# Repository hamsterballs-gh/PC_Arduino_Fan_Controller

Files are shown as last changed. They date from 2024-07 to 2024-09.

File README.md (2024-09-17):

# PC_Arduino_Fan_Controller
Arduino Fan and RGB Controller

A repository in shambles!
This is heavily under construction and many things are yet to be added/fixed/sorted out.

This project is for an Arduino-Nano based Fan and RGB controller, to fit in an old repurposed DVD Drive cage.

Hardware features:
- It can control 6 fans with PWM, of which channels 1-4 can use variable voltage DC.
- It controls three separate 12v RGB channels. 2 are 12v, and 1 is 5v for LEDs to fit in the case.
- RGB hard drive light - Two 2-pin connectors are used to use 2 HDD light inputs (I have a SAS card with a HDD light output). This controls the second 5v output.
- Support for 4 temperature sensors.
- Infra-red remote support, currently set to use the 44 button remotes that come with cheap Chinese RGB kits.
- Light sensor for auto LCD screen dimming.
- 16x2 I2C LCD display, to display messages.
- Read fan RPM from all channels.
- Serial communication to PC over USB.
- FRAM and EEPROM used for storing settings. EEPROM is used as a backup but must be restored manually with a serial command.
- A buzzer for alerts. I have not programmed this yet.
- Red LED indicator, typically lit up for serial transfers, IR commands and it will flash if the scheduler runs behind.
- Real-time clock so the fan controller can display the time even after being powered off.

Code features:
- Can set custom fan profiles, set using an average of 8 temperature inputs (4 built-in and overrideable, 8 can be sent from the computer).
    - Specifically, fans can all be set from 0 to 100%, regardless of temperature.
- Can set custom RGB profiles, including a 10 colour sequence, or a range of random values.
- Can send messages to the LCD display.
- Can custom strings for the fan controller.
- Can read fan RPM and temperature values to PC.

State of things:
- Most of the Arduino code is feature complete.
- The PCB design needs to be updated, but can be bodged to a working state.
- Component values are often incorrect. A parts list needs to be made.
- Basic Python Serial interaction is mostly working.

Next major tasks:
- Improve documentation and add a creation/installation guide.
- Create a GUI in Python to enable easy setting of RGB and fan profiles, and read data.

If you have taken an interest in this project and something's not right, please raise an issue.
That way I should get an email and I will respond as soon as I can.

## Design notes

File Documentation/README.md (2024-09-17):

# Documentation

This is where the documentation lives.
Information such as how to use the RGB remote, installation and hardware modifications.

### Arduino Modifications
- Information on modifications suggested for the Arduino Nano

### Remote Control
- A brief description on what every button does

### Components
- A list of components required for the project

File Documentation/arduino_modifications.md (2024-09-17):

# Arduino Modifications

## Disable auto-reset on serial connection
- The Arduino Nano will reset on any serial connection being established.
- Remove the indicated capacitor to disable this.
- Tweezers and a soldering iron are recommended.
- Note that the exact location of the capacitor can differ on Nano variants.

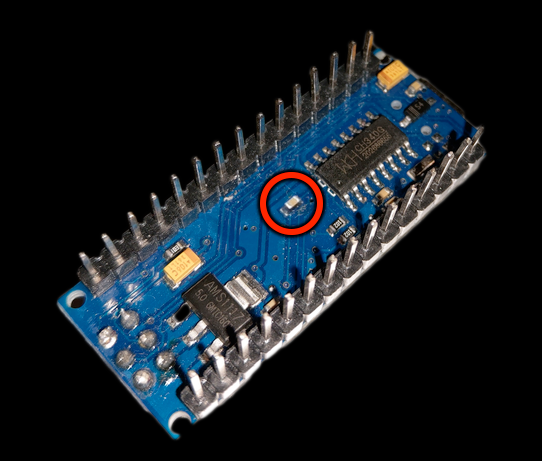
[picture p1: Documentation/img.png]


## Prevent USB backpower to 5v and 12v rails
- The Arduino Nano allows the USB input to backpower the 5v and Vin pins.
- If connected with USB to a computer where the USB ports remain powered on shutdown, backpowering can occur.
- This may damage the Arduino and/or the computer, or result in unwanted behaviour.
- Remove the indicated diode to prevent this.
- Tweezers and a soldering iron are recommended.
- Note that the exact location of the diode can differ on Nano variants.

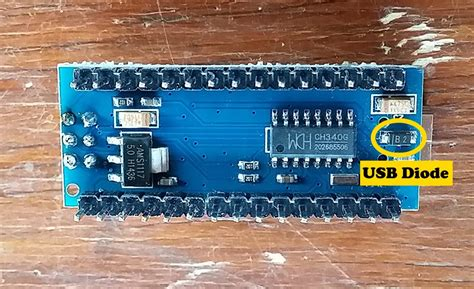
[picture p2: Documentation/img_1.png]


## Warning
- Please note that these changes are easy to perform, but reversing them takes skill in small-scale soldering.
- For the regular user, please understand that this is essentially a permanent modification of the Nano.

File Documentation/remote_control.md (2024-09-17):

# Remote Control Scheme

## Using: RGB 44 button remote

### Brightness Up:
- Increase brightness on selected RGB channel
- If all channels selected, channels 2 and 3 will be set to power LED channel brightness
### Brightness Down:
- Decrease brightness on selected RGB channel
- If all channels selected, channels 2 and 3 will be set to power LED channel brightness
### Pause:
- Pauses and resumes dynamic RGB profiles on selected channels
### Power:
- Turns on/off selected RGB channel
- Power and HDD LED outputs will be set to minimum brightness, but not off
- If all channels selected, channels 2 and 3 will be set to power LED channel power state
### Colour buttons:
- Load the set profile for the button on the selected RGB channels
- By default, this will be colours to closely match the buttons, and will be static
### Red/Green/Blue up buttons:
- If a static RGB profile is selected, the Red/Green/Blue value will be increased
- If a random colour, dynamic RGB channel is selected, this will increase the minimum random value of the associated chosen colour
### Quick:
- Speed will be increased on selected RGB channels using a dynamic RGB profile
### Red/Green/Blue down buttons:
- If a static RGB profile is selected, the Red/Green/Blue value will be decreased
- If a random colour, dynamic RGB channel is selected, this will decrease the minimum random value of the associated chosen colour
### Slow:
- Speed will be decreased on selected RGB channels using a dynamic RGB profile
### DIY 1/2/3:
- Select individual RGB channels 1/2/3
### Auto:
- Change inbuilt LCD display to next mode
### DIY 4:
- If RGB channels 2 or 3 are selected, set these channels to match RGB of channel 1
- Brightness of the channel will remain unchanged
### DIY 5:
- If RGB channel 3 is selected, set this channel to match RGB of channel 2
- Brightness of the channel will remain unchanged
### DIY 6:
- Select all RGB channels
### Flash:
- Load the 'flash' RGB profile on the selected RGB channels
### Jump 3:
- Load the RGB profile on the selected RGB channels
- By default, this will display red, green and blue colours in a repeating pattern
### Jump 7:
- Load the RGB profile on the selected RGB channels
- By default, this will display a random colour on each colour change
### Fade 3:
- Load the RGB profile on the selected RGB channels
- By default, this will display red, green and blue in a repeating pattern with a smooth transition
### Fade 7:
- Load the RGB profile on the selected RGB channels
- By default, this will display a random colour on each colour change with a smooth transition

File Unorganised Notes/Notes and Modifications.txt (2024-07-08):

########################################
# Arduino Fan Controller Modifications #
########################################

Things that aren't in the other notes but may be important:

1) Laziness
	Currently, my organisation on this project is in shambles.
	Documentation is imaginary, at best.

2) Backpowering
	If the connected USB port remains powered when PC is off, the Arduino will remain on.
	Add a diode from the 12v molex to Vin on the Arduino
	- this will prevent backpowering to the PC 12v rail.
	Ideally, a reset trigger needs to be put in place when the 12v powers up on computer reboot.

3) Wire bodging
	As shown in one of the pictures, the output wiring from the ATTiny85s are wrong.
	This requires a fix in the PCB design but this hasn't been done yet.

4) Fritzing
	The Adafruit parts library was used.
	This may have been updated.

5) Python libraries
	Installation of psutil and GPUtil are required for pc_status_130 to display all information.
	PySerial is used.

6) Arduino libraries
	LCD by Blackhawk
	Adafruit BusIO and PWM driver for PCA9685
	IRRemote

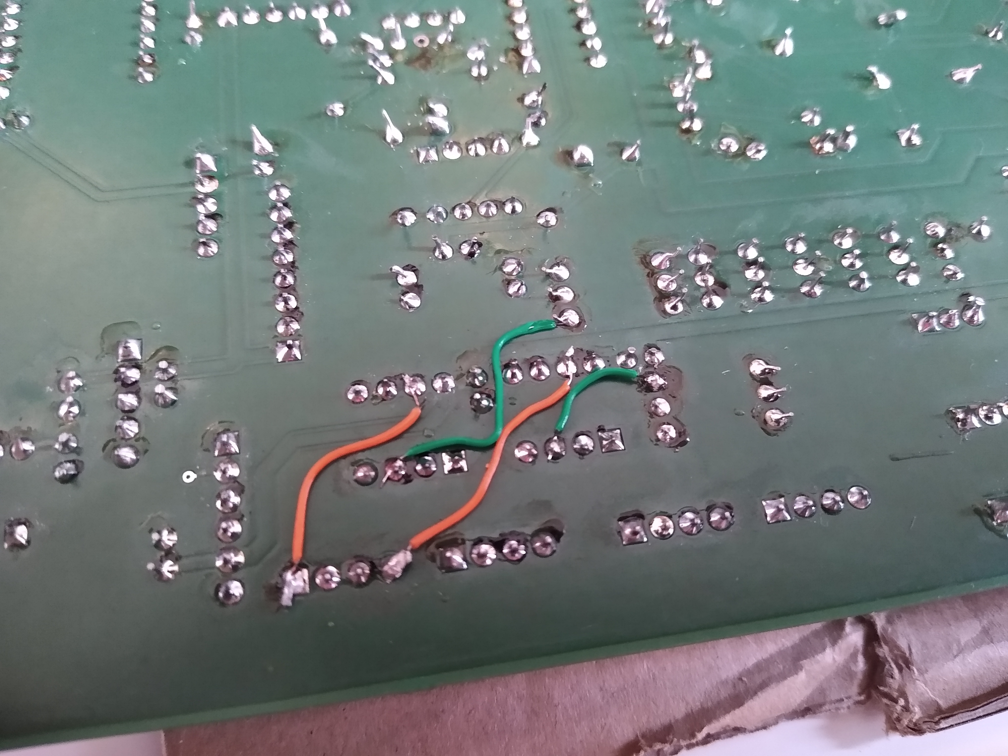
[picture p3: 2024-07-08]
Pictures/ATTiny85 bodge wires.jpg

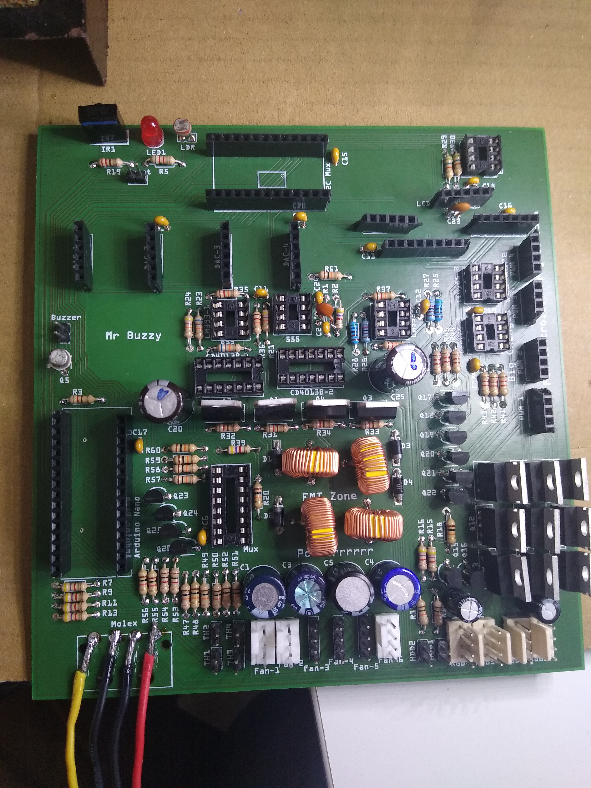
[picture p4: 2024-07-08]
Pictures/Semi-populated PCB.jpg

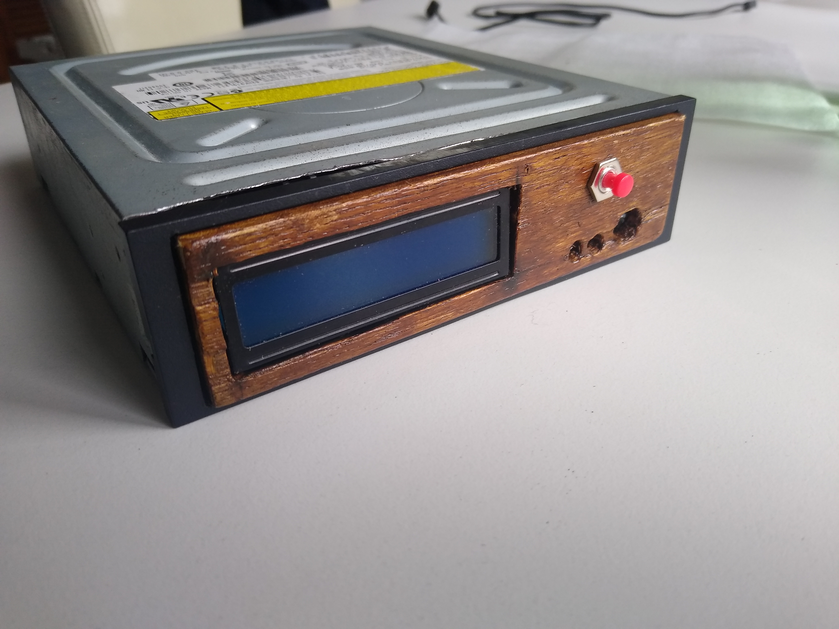
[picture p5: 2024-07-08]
Pictures/DVD housing.jpg

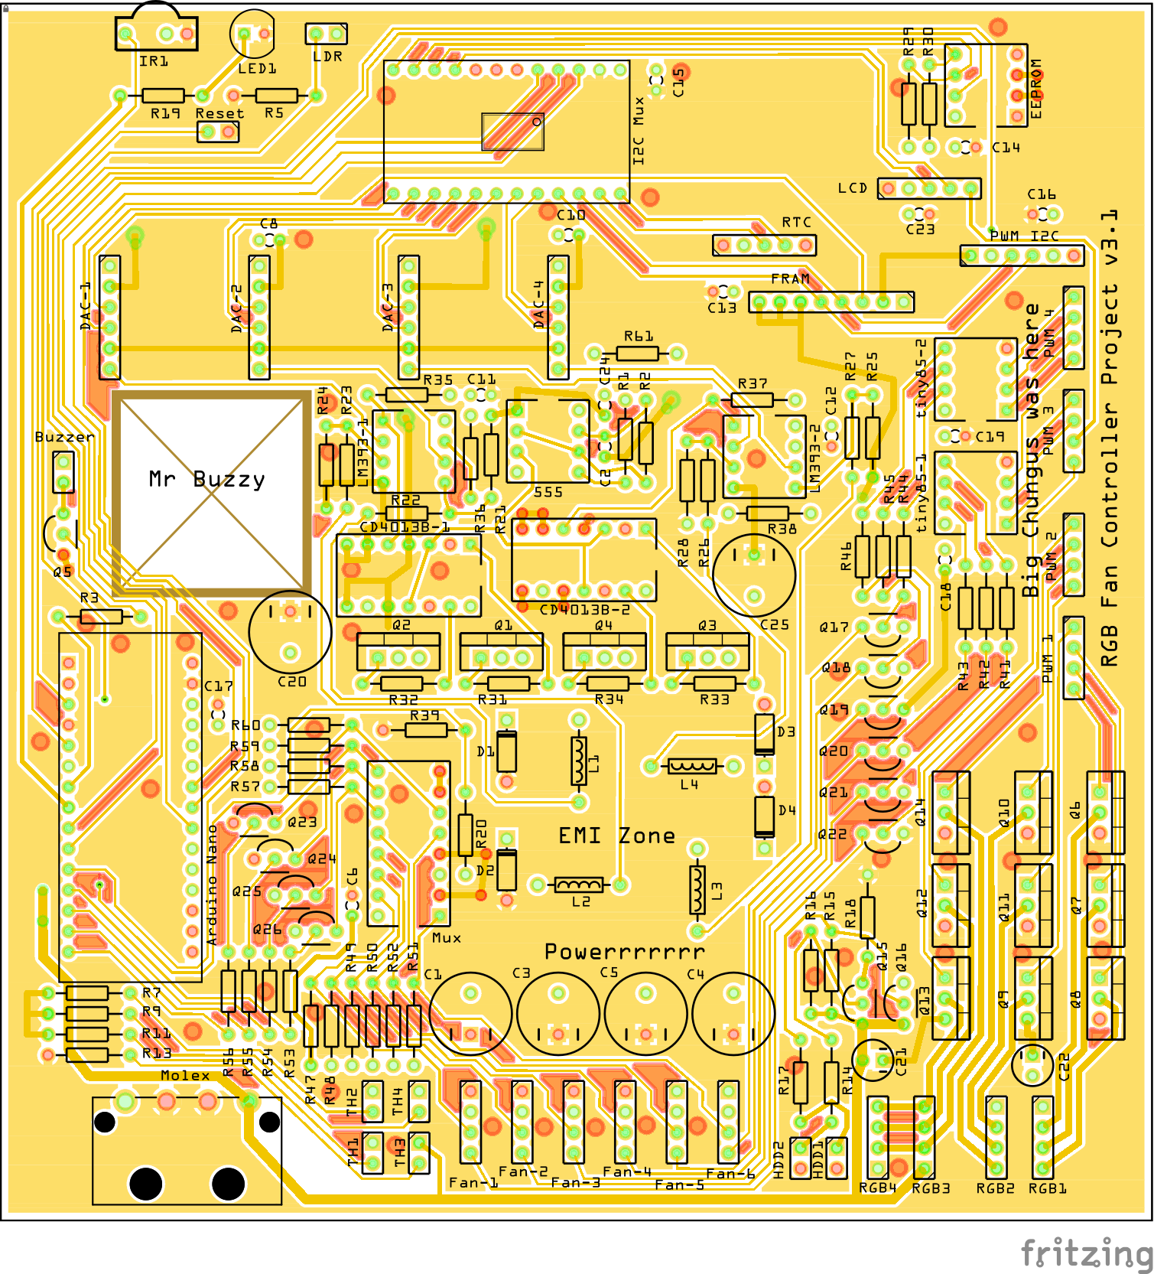
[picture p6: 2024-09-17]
Fritzing/PCB Images/Controller_v3 6.3.4 pcb_top.png

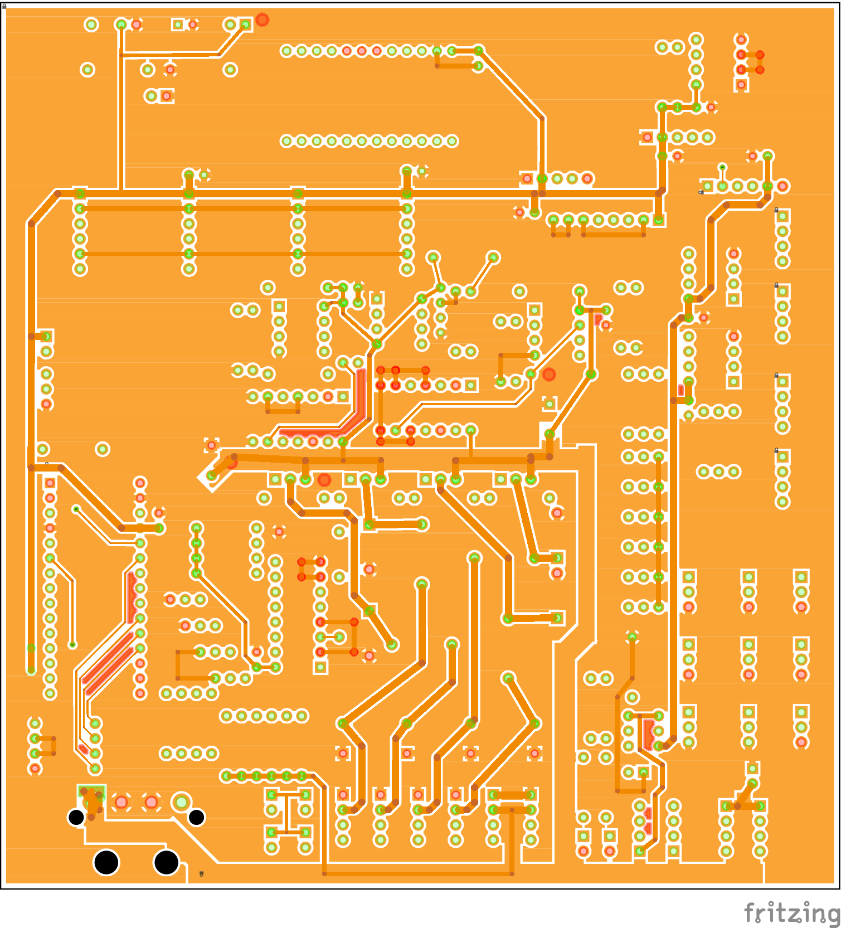
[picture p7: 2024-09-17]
Fritzing/PCB Images/Controller_v3 6.3.4 pcb_bottom.png

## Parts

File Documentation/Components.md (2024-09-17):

# Components

## Separate parts to install on completed PCB
- Arduino Nano - 5 volt version
- Adafruit MCP4725 (4x) - original and new versions fit PCB
- Adafruit TCA9548A
- 24LC256
- Adafruit PCF8523
- Adafruit I2C FRAM - MB85RC256
- Adafruit PCA9685
- LM393 (2x)
- NE555
- CD4013B
- ATtiny85 (2x) - require separate programming
- 16x2 LCD with I2C Backpack
- CD4051BE

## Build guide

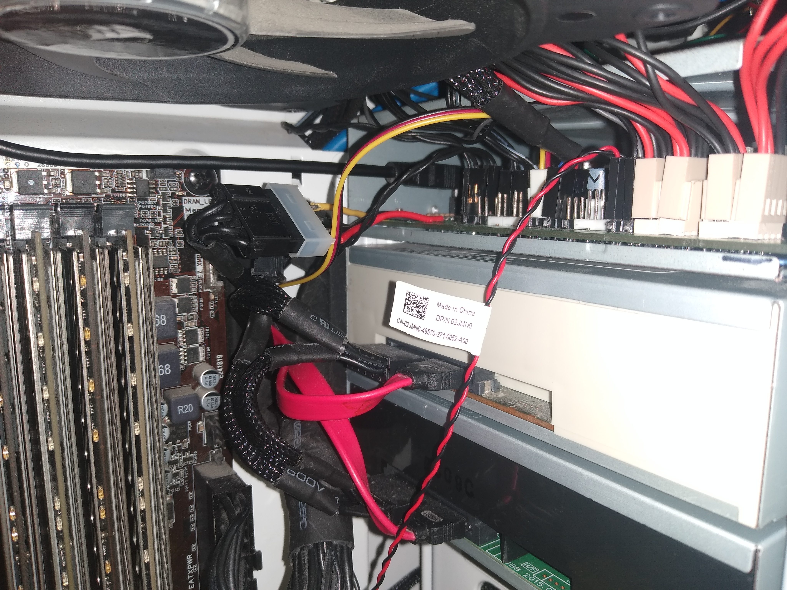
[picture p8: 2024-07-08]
Pictures/Installation cable mess.jpg

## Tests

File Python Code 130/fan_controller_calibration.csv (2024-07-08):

Description | Low reading | Low value | High reading | High value
Thermistor 1 | 128 | 0 | 830 | 100
Thermistor 2 | 128 | 0 | 830 | 100
Thermistor 3 | 128 | 0 | 830 | 100
Thermistor 4 | 128 | 0 | 830 | 100
LDR | 0 | 0 | 1023 | 1023

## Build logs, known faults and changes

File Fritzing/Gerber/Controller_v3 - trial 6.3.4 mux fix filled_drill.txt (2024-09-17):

; NON-PLATED HOLES START AT T1
; THROUGH (PLATED) HOLES START AT T100
M48
INCH
T1C0.100000
T2C0.157000
T100C0.040000
T101C0.038000
T102C0.060000
T103C0.042000
T104C0.042251
T105C0.015748
T106C0.035000
T107C0.031497
T108C0.036000
T109C0.030000
T110C0.039370
%
T1
X005076Y004802
X013076Y004802
T2
X011076Y001802
X007076Y001802
T100
X028076Y024302
X026076Y016302
X031576Y022052
X030076Y016302
X033826Y014052
X035576Y022052
X028076Y020302
X033826Y018052
T101
X018076Y003802
X032826Y004302
X022826Y006302
X025326Y004302
X048076Y046802
X050576Y002552
X044826Y004552
X032826Y003302
X027076Y043302
X012576Y045302
X052076Y033802
X005326Y043302
X030326Y005302
X051076Y046802
X027826Y005302
X040576Y003552
X041826Y044552
X045076Y050052
X046076Y050052
X022826Y004302
X030326Y003302
X012576Y044302
X052076Y028802
X042576Y005552
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

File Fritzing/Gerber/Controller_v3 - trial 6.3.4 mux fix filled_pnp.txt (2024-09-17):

*Pick And Place List
*Company=
*Author=
*eMail=
*
*Project=Controller_v3 - trial 6.3.4 mux fix filled
*Date=23:15:45
*CreatedBy=Fritzing 0.9.6b.2021-02-21.CD-175-0-8a1e0682
*
*
*Coordinates in mm, always center of component
*Origin 0/0=Lower left corner of PCB
*Rotation in degree (0-360, math. pos.)
*
*No;Value;Package;X;Y;Rotation;Side;Name
1;;;101.981;-29.8072;0;Bottom;Copper Fill256
2;;;120.193;-133.109;0;Bottom;Copper Fill333
3;;;62.1538;-10.554;0;Bottom;Copper Fill283
4;220;THT;38.2953;-58.5532;180;Bottom;R59
5;;;9.271;-61.1254;0;Bottom;Copper Fill365
6;;;26.8478;-64.5417;0;Bottom;Copper Fill328
7;;;126.53;-46.7998;0;Bottom;Copper Fill107
8;;;106.845;-43.6502;0;Bottom;Copper Fill357
9;;;43.7388;-94.2724;0;Bottom;Copper Fill174
10;;;126.301;-123.978;0;Bottom;Copper Fill62
11;100nF;100 mil [THT, multilayer];116.4;-81.4132;-90;Bottom;C18
12;;;135.509;-64.9354;0;Bottom;Copper Fill213
13;;THT;70.6803;-12.1982;0;Bottom;Fan-3
14;;;53.4924;-139.535;0;Bottom;Copper Fill140
15;;;87.8078;-113.64;0;Bottom;Copper Fill386
16;;;43.3578;-41.0467;0;Bottom;Copper Fill22
17;;;89.5096;-108.369;0;Bottom;Copper Fill180
18;0.22mF;200 mil [THT, electrolytic];57.9803;-25.5332;-90;Bottom;C1
19;220;THT;124.02;-75.6982;90;Bottom;R41
20;;;123.99;-108.42;0;Bottom;Copper Fill72
21;;;114.097;-101.359;0;Bottom;Copper Fill177
22;;;27.813;-138.583;0;Bottom;Copper Fill65
23;;;8.7884;-68.1358;0;Bottom;Copper Fill199
24;220;THT;77.0303;-96.0182;-90;Bottom;R1
25;;THT;94.1753;-120.148;-90;Bottom;RTC
26;;;86.9315;-114.453;0;Bottom;Copper Fill387
27;10k;THT;50.3603;-101.733;180;Bottom;R35
28;;;31.7246;-50.4574;0;Bottom;Copper Fill235
29;;;123.99;-94.4502;0;Bottom;Copper Fill346
30;;;45.593;-57.6202;0;Bottom;Copper Fill225
31;;THT;83.3803;-12.1982;0;Bottom;Fan-5
32;;;127.165;-21.4252;0;Bottom;Copper Fill373
33;;;116.37;-23.9398;0;Bottom;Copper Fill104
34;;;62.4078;-40.5641;0;Bottom;Copper Fill30
35;;400 mil [THT];85.2853;-56.0132;180;Bottom;L4
36;;THT;51.6303;-14.7382;0;Bottom;TH4
37;;;114.833;-133.338;0;Bottom;Copper Fill143
38;;400 mil [THT];71.3153;-41.4082;0;Bottom;L2
39;;;73.8378;-142.647;0;Bottom;Copper Fill46
40;;;75.2856;-94.1454;0;Bottom;Copper Fill29
41;;;63.3857;-54.1404;0;Bottom;Copper Fill301
42;220;THT;62.4253;-66.1732;0;Bottom;R31
43;;THT;89.7303;-12.1982;0;Bottom;Fan-6
44;;;55.6768;-66.815;0;Bottom;Copper Fill5
45;;;97.9678;-34.7348;0;Bottom;Copper Fill252
46;;TO92 [THT];108.59;-67.9893;0;Bottom;Q18
47;;THT;108.145;-10.2932;180;Bottom;RGB4
48;;;48.133;-25.4638;0;Bottom;Copper Fill264
49;220;THT;33.8503;-138.563;0;Bottom;R5
50;;;24.511;-66.2054;0;Bottom;Copper Fill327
51;;;79.5401;-23.9652;0;Bottom;Copper Fill318
52;220;THT;38.2953;-56.0132;180;Bottom;R58
53;;;109.652;-19.8631;0;Bottom;Copper Fill363
54;;THT;113.86;-10.2932;180;Bottom;RGB3
55;;;135.433;-22.5936;0;Bottom;Copper Fill272
56;;;127.165;-21.4252;0;Bottom;Copper Fill113
57;;;12.6746;-104.102;0;Bottom;Copper Fill170
58;;;34.4678;-119.99;0;Bottom;Copper Fill348
59;;;86.9315;-114.453;0;Bottom;Copper Fill131
60;;;68.2244;-10.8588;0;Bottom;Copper Fill284
61;;;25.5778;-13.4623;0;Bottom;Copper Fill92
62;;;77.0128;-17.0183;0;Bottom;Copper Fill103
63;;THT;98.6203;-7.75323;0;Bottom;HDD2
64;;;84.3026;-83.7568;0;Bottom;Copper Fill2
65;;;27.2288;-55.7152;0;Bottom;Copper Fill227
66;;THT;132.275;-109.988;0;Bottom;PWM 4
67;;;23.0378;-147.181;0;Bottom;Copper Fill81
68;;;44.958;-42.6088;0;Bottom;Copper Fill233
69;;;56.388;-90.691;0;Bottom;Copper Fill187
70;;;113.462;-103.239;0;Bottom;Copper Fill173
71;;;120.193;-131.407;0;Bottom;Copper Fill57
72;;;53.6956;-143.65;0;Bottom;Copper Fill142
73;;THT;26.8653;-134.118;90;Bottom;Reset
74;;;79.5401;-23.9652;0;Bottom;Copper Fill40
75;;;129.007;-96.5584;0;Bottom;Copper Fill183
76;;300 mil [THT];94.1753;-49.6886;-90;Bottom;D4
77;;;93.7641;-82.0677;0;Bottom;Copper Fill377
78;;;18.7198;-21.6538;0;Bottom;Copper Fill275
79;47k;THT;107.51;-96.6532;90;Bottom;R25
80;;THT;45.9153;-14.7382;0;Bottom;TH2
81;;TO220 [THT];136.974;-50.2982;90;Bottom;Q6
82;;;35.7505;-74.2191;0;Bottom;Copper Fill383
83;;;104.75;-110.833;0;Bottom;Copper Fill168
84;;;83.693;-85.8777;0;Bottom;Copper Fill380
85;;TO92 [THT];7.7264;-84.7787;90;Bottom;Q5
86;;;57.9501;-23.9652;0;Bottom;Copper Fill25
87;;;12.0904;-111.316;0;Bottom;Copper Fill166
88;100nF;100 mil [THT, multilayer];80.8403;-140.468;-90;Bottom;C15
89;;DIP (Dual Inline) [THT];71.9503;-81.4132;90;Bottom;CD4013B-2
90;220;THT;38.2953;-61.0932;180;Bottom;R60
91;;;110.312;-90.4116;0;Bottom;Copper Fill188
92;;;16.0782;-43.955;0;Bottom;Copper Fill229
93;;;61.2902;-21.6538;0;Bottom;Copper Fill273
94;;;62.0522;-15.4816;0;Bottom;Copper Fill282
95;;THT;125.925;-118.878;-90;Bottom;PWM I2C
96;;TO220 [THT];49.0903;-70.8722;0;Bottom;Q2
97;;;5.9055;-19.6218;0;Bottom;Copper Fill341
98;;;80.8736;-16.4214;0;Bottom;Copper Fill276
99;;;80.4418;-23.0381;0;Bottom;Copper Fill321
100;;TO220 [THT];117.924;-38.8682;90;Bottom;Q12
101;220;THT;87.8253;-66.1732;0;Bottom;R33
102;;;126.53;-23.9398;0;Bottom;Copper Fill109
103;100nF;100 mil [THT, multilayer];70.0453;-121.418;180;Bottom;C10
104;;;107.747;-32.6774;0;Bottom;Copper Fill277
105;;;48.8442;-44.1582;0;Bottom;Copper Fill241
106;;;113.767;-129.147;0;Bottom;Copper Fill148
107;;;92.8751;-83.0202;0;Bottom;Copper Fill114
108;;;78.613;-23.0381;0;Bottom;Copper Fill42
109;68k;THT;104.97;-96.6532;90;Bottom;R27
110;220;THT;49.7253;-66.1732;180;Bottom;R32
111;;THT;45.9153;-8.38823;0;Bottom;TH1
112;;;14.097;-23.6858;0;Bottom;Copper Fill10
113;;;106.845;-41.8214;0;Bottom;Copper Fill88
114;;;129.311;-104.483;0;Bottom;Copper Fill172
115;;;5.2752;-40.7733;0;Bottom;Via8
116;;;47.1678;-59.6014;0;Bottom;Copper Fill19
117;;;37.338;-37.4526;0;Bottom;Copper Fill249
118;;;123.088;-55.766;0;Bottom;Copper Fill219
119;;;91.9607;-82.0677;0;Bottom;Copper Fill115
120;;;116.688;-91.1482;0;Bottom;Copper Fill200
121;;;32.5755;-147.028;0;Bottom;Copper Fill323
122;;;129.946;-79.7182;0;Bottom;Copper Fill198
123;;;48.514;-41.9484;0;Bottom;Copper Fill246
124;;;48.2854;-111.621;0;Bottom;Copper Fill164
125;;;123.99;-94.4502;0;Bottom;Copper Fill73
126;;;45.9486;-25.1336;0;Bottom;Copper Fill263
127;;;48.0441;-60.5031;0;Bottom;Copper Fill303
128;;;34.8107;-75.0954;0;Bottom;Copper Fill384
129;;;12.2682;-74.181;0;Bottom;Copper Fill218
130;;;89.7128;-17.0183;0;Bottom;Copper Fill378
131;;;118.91;-97.5617;0;Bottom;Copper Fill342
132;;;21.8059;-14.7831;0;Bottom;Copper Fill124
133;;computer-peripheral-power-ra;23.0553;-9.09943;180;Bottom;Molex
134;;;29.2862;-25.2606;0;Bottom;Copper Fill268
135;100nF;100 mil [THT, multilayer];59.2503;-101.733;180;Bottom;C11
136;;;60.5028;-102.642;0;Bottom;Copper Fill138
137;220;THT;33.2153;-28.0732;-90;Bottom;R54
138;10k;THT;94.8103;-87.1282;180;Bottom;R38
139;;;64.008;-136.614;0;Bottom;Copper Fill146
140;;;135.42;-23.9398;0;Bottom;Copper Fill110
141;;THT;77.0303;-12.1982;0;Bottom;Fan-4
142;;;21.8059;-14.7831;0;Bottom;Copper Fill392
143;220;THT;118.94;-75.6982;90;Bottom;R43
144;;;48.0441;-60.5031;0;Bottom;Copper Fill21
145;;;51.5366;-104.001;0;Bottom;Copper Fill160
146;;;6.1214;-63.7162;0;Bottom;Copper Fill216
147;0.22mF;200 mil [THT, electrolytic];90.3653;-25.5332;-90;Bottom;C4
148;;;61.3791;-39.5481;0;Bottom;Copper Fill308
149;;;118.694;-87.3382;0;Bottom;Copper Fill193
150;;;74.5236;-11.189;0;Bottom;Copper Fill285
151;68k;THT;50.3603;-87.1282;180;Bottom;R22
152;;;105.931;-42.7231;0;Bottom;Copper Fill359
153;0.22µF;100 mil [THT, electrolytic];107.51;-19.8182;180;Bottom;C21
154;;THT;121.48;-139.833;180;Bottom;EEPROM
155;;;34.4678;-121.692;0;Bottom;Copper Fill75
156;;;109.525;-5.9312;0;Bottom;Copper Fill298
157;;;34.8107;-75.0954;0;Bottom;Copper Fill127
158;;;79.5401;-22.1618;0;Bottom;Copper Fill41
159;10k;THT;40.8353;-24.2632;90;Bottom;R48
160;;;56.9976;-123.609;0;Bottom;Copper Fill154
161;;;22.7584;-66.2054;0;Bottom;Copper Fill51
162;;dip;120.21;-89.6682;180;Bottom;tiny85-1
163;;;118.91;-95.8599;0;Bottom;Copper Fill70
164;;;70.993;-75.0192;0;Bottom;Copper Fill13
165;;;73.025;-95.1106;0;Bottom;Copper Fill186
166;;TO92 [THT];34.0408;-44.6721;180;Bottom;Q24
167;2.2k;THT;111.955;-137.293;-90;Bottom;R29
168;;;71.2978;-122.314;0;Bottom;Copper Fill78
169;;;103.937;-31.2042;0;Bottom;Copper Fill255
170;;;16.0703;-50.9247;0;Bottom;Arduino Nano
171;;;19.6596;-23.2286;0;Bottom;Copper Fill270
172;;;62.4078;-38.5575;0;Bottom;Copper Fill307
173;;;110.998;-10.2746;0;Bottom;Copper Fill296
174;;;88.0999;-120.168;0;Bottom;Copper Fill335
175;;;134.925;-42.7358;0;Bottom;Copper Fill239
176;220;THT;111.32;-82.0482;90;Bottom;R44
177;;;116.37;-35.3698;0;Bottom;Copper Fill105
178;;;60.5028;-102.642;0;Bottom;Copper Fill393
179;;;110.998;-12.8146;0;Bottom;Copper Fill288
180;;;114.478;-123.139;0;Bottom;Copper Fill355
181;;;29.845;-111.621;0;Bottom;Copper Fill163
182;;;125.26;-135.166;0;Bottom;Copper Fill388
183;;;35.2933;-120.803;0;Bottom;Copper Fill349
184;;;112.166;-89.7766;0;Bottom;Copper Fill189
185;;;116.37;-79.3499;0;Bottom;Copper Fill74
186;;;23.0378;-147.181;0;Bottom;Copper Fill351
187;220;THT;12.2603;-74.4282;0;Bottom;R3
188;;;107.734;-42.7231;0;Bottom;Copper Fill90
189;;;39.243;-87.7827;0;Bottom;Copper Fill118
190;;;90.0684;-100.165;0;Bottom;Copper Fill179
191;;TO220 [THT];128.084;-50.2982;90;Bottom;Q10
192;;;99.7966;-115.812;0;Bottom;Copper Fill162
193;;TO92 [THT];108.59;-52.7493;0;Bottom;Q21
194;2.2k;THT;114.495;-137.293;-90;Bottom;R30
195;;;52.5272;-124.244;0;Bottom;Copper Fill152
196;;;106.172;-63.1828;0;Bottom;Copper Fill214
197;;;72.1233;-121.438;0;Bottom;Copper Fill80
198;;;52.4256;-40.5006;0;Bottom;Copper Fill242
199;;;106.172;-67.9072;0;Bottom;Copper Fill207
200;;;92.8751;-83.0202;0;Bottom;Copper Fill374
201;;TO92 [THT];108.59;-57.8293;0;Bottom;Q20
202;;TO92 [THT];31.5008;-49.1171;180;Bottom;Q23
203;;;61.3156;-101.753;0;Bottom;Copper Fill394
204;;;118.58;-118.898;0;Bottom;Copper Fill389
205;;;47.1678;-90.0814;0;Bottom;Copper Fill23
206;;;118.58;-118.898;0;Bottom;Copper Fill137
207;;THT;31.9453;-111.258;0;Bottom;DAC-2
208;;;35.2933;-120.803;0;Bottom;Copper Fill77
209;;;63.3857;-39.5481;0;Bottom;Copper Fill33
210;47k;THT;84.6503;-90.9382;-90;Bottom;R28
211;;;54.1528;-56.3502;0;Bottom;Copper Fill299
212;;;73.8378;-140.894;0;Bottom;Copper Fill47
213;;;121.564;-60.592;0;Bottom;Copper Fill215
214;10k;THT;50.9953;-24.2632;90;Bottom;R51
215;;;112.192;-47.8031;0;Bottom;Copper Fill364
216;;;68.7451;-23.9652;0;Bottom;Copper Fill310
217;;;66.675;-111.265;0;Bottom;Copper Fill167
218;;;108.382;-91.5927;0;Bottom;Copper Fill119
219;;;90.3351;-23.9652;0;Bottom;Copper Fill36
220;;;52.5526;-26.0988;0;Bottom;Copper Fill266
221;;;48.7172;-8.395;0;Bottom;Copper Fill294
222;;;25.5778;-13.4623;0;Bottom;Copper Fill361
223;;;120.752;-113.729;0;Bottom;Copper Fill161
224;;;80.8228;-138.379;0;Bottom;Copper Fill329
225;;;12.2602;-41.4083;0;Bottom;Via11
226;;;108.42;-127.153;0;Bottom;Copper Fill84
227;;;26.8859;-14.7831;0;Bottom;Copper Fill94
228;220;THT;10.9903;-20.4532;180;Bottom;R13
229;;;54.7624;-123.914;0;Bottom;Copper Fill153
230;;;126.53;-35.3698;0;Bottom;Copper Fill371
231;;;77.724;-123.914;0;Bottom;Copper Fill157
232;;THT;132.275;-97.2882;0;Bottom;PWM 3
233;;;30.353;-44.6281;0;Bottom;Copper Fill132
234;;;23.9649;-146.19;0;Bottom;Copper Fill83
235;;;74.803;-93.5104;0;Bottom;Copper Fill185
236;;;62.4078;-55.1564;0;Bottom;Copper Fill15
237;;;116.37;-46.7998;0;Bottom;Copper Fill106
238;47k;THT;60.5203;-94.1132;-90;Bottom;R21
239;;;25.908;-72.1998;0;Bottom;Copper Fill205
240;;;8.8392;-89.0146;0;Bottom;Copper Fill191
241;;;86.5632;-11.7478;0;Bottom;Copper Fill287
242;;;29.6418;-138.583;0;Bottom;Copper Fill340
243;;;27.9654;-41.5674;0;Bottom;Copper Fill236
244;;;32.893;-63.2844;0;Bottom;Copper Fill203
245;;;24.1935;-14.7831;0;Bottom;Copper Fill362
246;10k;THT;78.3003;-106.813;0;Bottom;R61
247;;;91.9607;-82.0677;0;Bottom;Copper Fill376
248;;THT;128.465;-10.2932;0;Bottom;RGB1
249;;;107.734;-42.7231;0;Bottom;Copper Fill360
250;;TO92 [THT];106.151;-26.9937;90;Bottom;Q15
251;;;32.5755;-145.428;0;Bottom;Copper Fill49
252;;;119.736;-96.6727;0;Bottom;Copper Fill344
253;;;89.7636;-120.993;0;Bottom;Copper Fill156
254;;;18.2372;-39.129;0;Bottom;Copper Fill7
255;;;63.3857;-54.1404;0;Bottom;Copper Fill17
256;100nF;100 mil [THT, multilayer];74.4903;-100.463;-90;Bottom;C24
257;;;31.4706;-25.6162;0;Bottom;Copper Fill267
258;220;THT;121.48;-75.6982;90;Bottom;R42
259;;TO220 [THT];117.924;-50.2982;90;Bottom;Q14
260;;;39.3446;-57.5694;0;Bottom;Copper Fill220
261;;;62.4253;-134.118;90;Bottom;I2C Mux
262;;;31.8008;-29.5786;0;Bottom;Copper Fill259
263;;;29.9212;-17.5898;0;Bottom;Copper Fill278
264;;;22.2504;-24.8288;0;Bottom;Copper Fill261
265;;;125.26;-144.59;0;Bottom;Copper Fill332
266;;;63.3857;-39.5481;0;Bottom;Copper Fill309
267;;;103.226;-95.4154;0;Bottom;Copper Fill135
268;100nF;100 mil [THT, multilayer];33.2153;-120.783;180;Bottom;C8
269;10k;THT;106.875;-37.5982;90;Bottom;R18
270;100nF;100 mil [THT, multilayer];113.225;-123.958;0;Bottom;C23
271;;;69.6341;-23.0381;0;Bottom;Copper Fill34
272;;;114.478;-123.139;0;Bottom;Copper Fill85
273;;;7.5184;-61.1254;0;Bottom;Copper Fill96
274;;400 mil [THT];71.3153;-56.6482;90;Bottom;L1
275;;;57.9628;-17.0183;0;Bottom;Copper Fill99
276;;;47.1678;-90.0814;0;Bottom;Copper Fill305
277;;;46.1772;-126.454;0;Bottom;Copper Fill149
278;;;95.1357;-63.6654;0;Bottom;Copper Fill45
279;;;83.693;-85.8777;0;Bottom;Copper Fill120
280;68k;THT;87.1903;-90.9382;-90;Bottom;R26
281;;;23.0378;-145.276;0;Bottom;Copper Fill82
282;;;39.6748;-85.611;0;Bottom;Copper Fill194
283;;;7.8153;-92.2082;0;Bottom;Buzzer
284;;;43.7134;-24.8288;0;Bottom;Copper Fill262
285;220;THT;28.1353;-28.0732;-90;Bottom;R56
286;;;89.7128;-17.0183;0;Bottom;Copper Fill116
287;;;12.8952;-64.2683;0;Bottom;Via12
288;;;126.34;-100.902;0;Bottom;Copper Fill178
289;;;106.782;-53.607;0;Bottom;Copper Fill228
290;;;28.7655;-137.706;0;Bottom;Copper Fill339
291;;;86.7918;-97.6252;0;Bottom;Copper Fill182
292;;;135.42;-46.7998;0;Bottom;Copper Fill112
293;;;94.1578;-52.5275;0;Bottom;Copper Fill314
294;;;109.525;-78.9308;0;Bottom;Copper Fill201
295;;;10.6934;-41.3896;0;Bottom;Copper Fill244
296;;;32.5755;-145.428;0;Bottom;Copper Fill324
297;;;106.845;-41.8214;0;Bottom;Copper Fill358
298;220;THT;106.24;-82.0482;90;Bottom;R46
299;100nF;100 mil [THT, multilayer];128.465;-123.958;0;Bottom;C16
300;;;64.3128;-17.0183;0;Bottom;Copper Fill101
301;;;123.99;-108.42;0;Bottom;Copper Fill345
302;;;27.6733;-63.6654;0;Bottom;Copper Fill54
303;;DIP (Dual Inline) [THT];50.3603;-79.5082;90;Bottom;CD4013B-1
304;220;THT;10.9903;-28.0732;180;Bottom;R7
305;;TO92 [THT];108.59;-73.0693;0;Bottom;Q17
306;;;121.361;-82.7662;0;Bottom;Copper Fill195
307;;;50.2412;-31.1026;0;Bottom;Copper Fill257
308;10k;THT;45.9153;-24.2632;90;Bottom;R50
309;;TO92 [THT];108.59;-47.6693;0;Bottom;Q22
310;;TO220 [THT];74.4903;-70.8722;0;Bottom;Q4
311;;;80.391;-11.4938;0;Bottom;Copper Fill286
312;;;79.9338;-139.218;0;Bottom;Copper Fill330
313;;;5.5626;-58.0012;0;Bottom;Copper Fill222
314;;;57.023;-23.0381;0;Bottom;Copper Fill27
315;;THT;68.7753;-111.258;0;Bottom;DAC-4
316;;THT;132.275;-82.0482;0;Bottom;PWM 2
317;;;127.165;-123.139;0;Bottom;Copper Fill337
318;;;80.7212;-127.14;0;Bottom;Copper Fill165
319;;;90.3351;-22.1618;0;Bottom;Copper Fill37
320;;;102.413;-94.5899;0;Bottom;Copper Fill134
321;;;5.9055;-29.0325;0;Bottom;Copper Fill67
322;;TO220 [THT];128.084;-27.4382;90;Bottom;Q9
323;;;127;-35.5222;0;Bottom;Copper Fill251
324;;;71.2978;-120.612;0;Bottom;Copper Fill79
325;;;41.4274;-100.622;0;Bottom;Copper Fill176
326;;;24.511;-66.2054;0;Bottom;Copper Fill52
327;;;111.531;-75.07;0;Bottom;Copper Fill204
328;;;127.247;-94.8944;-90;Bottom;TXT1
329;;;87.8078;-115.342;0;Bottom;Copper Fill129
330;;;80.4418;-23.0381;0;Bottom;Copper Fill43
331;;300 mil [THT];94.1753;-59.8486;-90;Bottom;D3
332;;;91.7194;-9.1316;0;Bottom;Copper Fill297
333;10k;THT;102.43;-17.2782;90;Bottom;R14
334;;;90.3351;-23.9652;0;Bottom;Copper Fill315
335;220;THT;75.1253;-66.1732;180;Bottom;R34
336;;;28.7655;-137.706;0;Bottom;Copper Fill64
337;;;108.788;-28.3594;0;Bottom;Copper Fill258
338;;;116.586;-34.8618;0;Bottom;Copper Fill247
339;;300 mil [THT];62.4253;-43.2878;90;Bottom;D2
340;220;THT;19.8803;-138.563;0;Bottom;R19
341;;;99.9744;-11.5954;0;Bottom;Copper Fill290
342;;;25.5064;-91.0799;0;Bottom;TXT2
343;;;23.9649;-146.19;0;Bottom;Copper Fill353
344;;;78.613;-23.0381;0;Bottom;Copper Fill320
345;;;29.0449;-134.138;0;Bottom;Copper Fill367
346;;;118.91;-97.5617;0;Bottom;Copper Fill69
347;;;41.783;-75.7304;0;Bottom;Copper Fill117
348;220;THT;108.78;-82.0482;90;Bottom;R45
349;;;127.165;-124.841;0;Bottom;Copper Fill336
350;;;75.4888;-121.069;0;Bottom;Copper Fill155
351;;;29.0449;-134.138;0;Bottom;Copper Fill100
352;;;24.1935;-14.7831;0;Bottom;Copper Fill93
353;;;63.6651;-100.8;0;Bottom;Copper Fill366
354;220;THT;35.7553;-28.0732;-90;Bottom;R53
355;;;41.0718;-57.5186;0;Bottom;Copper Fill224
356;;;46.609;-79.515;0;Bottom;Copper Fill197
357;;;129.667;-81.8772;0;Bottom;Copper Fill196
358;100nF;100 mil [THT, multilayer];118.945;-132.213;180;Bottom;C14
359;;dip;120.21;-103.638;180;Bottom;tiny85-2
360;;TO92 [THT];108.59;-62.9093;0;Bottom;Q19
361;;;32.893;-40.1831;0;Bottom;Copper Fill133
362;;;76.0216;-47.178;0;Bottom;TXT3
363;;;115.113;-84.3918;0;Bottom;Copper Fill4
364;;;73.8378;-140.894;0;Bottom;Copper Fill322
365;;;116.37;-79.3499;0;Bottom;Copper Fill347
366;;;32.5755;-147.028;0;Bottom;Copper Fill48
367;;;26.0698;-89.5663;0;Top;blkr13
368;10k;THT;38.2953;-24.2632;90;Bottom;R47
369;220;THT;30.6753;-28.0732;-90;Bottom;R55
370;;THT;102.43;-113.163;90;Bottom;FRAM
371;;;109.703;-26.0734;0;Bottom;Copper Fill9
372;;;50.3428;-124.575;0;Bottom;Copper Fill151
373;;;121.006;-132.233;0;Bottom;Copper Fill58
374;;;9.8552;-39.3322;0;Bottom;Copper Fill248
375;220;THT;10.9903;-22.9932;180;Bottom;R11
376;;;61.3156;-101.753;0;Bottom;Copper Fill139
377;100nF;100 mil [THT, multilayer];26.8653;-62.3632;90;Bottom;C17
378;;;109.474;-10.3;0;Bottom;Copper Fill12
379;;;10.4902;-36.9446;0;Bottom;Copper Fill250
380;;;7.8105;-81.1914;0;Bottom;Copper Fill63
381;;;33.3502;-146.203;0;Bottom;Copper Fill325
382;;TO92 [THT];39.1208;-35.7821;180;Bottom;Q26
383;;;24.638;-62.751;0;Bottom;Copper Fill206
384;;;35.7505;-74.2191;0;Bottom;Copper Fill126
385;;;23.0378;-145.276;0;Bottom;Copper Fill352
386;;;81.6356;-139.218;0;Bottom;Copper Fill331
387;;;42.7736;-12.5098;0;Bottom;Copper Fill289
388;;;51.5366;-143.98;0;Bottom;Copper Fill141
389;;;62.4078;-40.5641;0;Bottom;Copper Fill306
390;;;19.1135;-14.7831;0;Bottom;Copper Fill123
391;;;129.007;-106.718;0;Bottom;Copper Fill171
392;10k;THT;57.9803;-94.1132;90;Bottom;R36
393;;;135.42;-46.7998;0;Bottom;Copper Fill372
394;;;69.6341;-23.0381;0;Bottom;Copper Fill313
395;;;126.009;-103.086;0;Bottom;Copper Fill175
396;;;127.165;-123.139;0;Bottom;Copper Fill61
397;;;36.6141;-75.0954;0;Bottom;Copper Fill385
398;;;33.3502;-146.203;0;Bottom;Copper Fill50
399;;;20.4978;-13.4623;0;Bottom;Copper Fill390
400;220;THT;38.2953;-53.4732;180;Bottom;R57
401;;;88.0999;-120.168;0;Bottom;Copper Fill59
402;;;128.676;-108.928;0;Bottom;Copper Fill169
403;;;125.26;-144.59;0;Bottom;Copper Fill55
404;;THT;103.065;-7.75323;0;Bottom;HDD1
405;;;135.42;-35.3698;0;Bottom;Copper Fill111
406;;;106.553;-58.3568;0;Bottom;Copper Fill223
407;;;107.594;-48.2222;0;Bottom;Copper Fill234
408;4.7k;THT;99.8903;-30.6132;-90;Bottom;R16
409;;;125.984;-89.1162;0;Bottom;Copper Fill192
410;;;112.801;-69.7868;0;Bottom;Copper Fill208
411;;;118.91;-95.8599;0;Bottom;Copper Fill343
412;;;120.193;-131.407;0;Bottom;Copper Fill334
413;;;116.37;-35.3698;0;Bottom;Copper Fill368
414;47;THT;57.3453;-47.7582;90;Bottom;R20
415;;TO92 [THT];36.5808;-40.2271;180;Bottom;Q25
416;;;54.1528;-56.3502;0;Bottom;Copper Fill14
417;;THT;40.2003;-146.183;90;Bottom;LDR
418;;;54.5084;-82.2074;0;Bottom;Copper Fill3
419;;;70.6628;-17.0183;0;Bottom;Copper Fill102
420;;;57.9501;-22.1618;0;Bottom;Copper Fill26
421;;400 mil [THT];85.9203;-40.7732;90;Bottom;L3
422;;;101.524;-95.4154;0;Bottom;Copper Fill381
423;0.22mF;200 mil [THT, electrolytic];92.9053;-79.5082;90;Bottom;C25
424;;;74.4728;-93.3199;0;Bottom;Copper Fill28
425;;;41.2242;-24.1176;0;Bottom;Copper Fill260
426;;;89.4207;-23.0381;0;Bottom;Copper Fill317
427;;;27.0002;-24.9812;0;Bottom;Copper Fill269
428;;TO220 [THT];117.924;-27.4382;90;Bottom;Q13
429;;;71.5518;-38.7226;0;Bottom;Copper Fill397
430;100nF;100 mil [THT, multilayer];102.43;-96.6532;-90;Bottom;C12
431;;DIP (Dual Inline) [THT];67.5053;-96.0182;0;Bottom;555
432;;;75.057;-16.0912;0;Bottom;Copper Fill280
433;;;106.845;-43.6502;0;Bottom;Copper Fill87
434;;;77.0156;-32.8846;0;Bottom;TXT3
435;;;36.6141;-75.0954;0;Bottom;Copper Fill128
436;;;50.3936;-25.7686;0;Bottom;Copper Fill265
437;;;126.301;-123.978;0;Bottom;Copper Fill338
438;;;93.4466;-122.162;0;Bottom;Copper Fill159
439;;;65.8876;-135.979;0;Bottom;Copper Fill147
440;;;136.973;-96.4339;-90;Bottom;TXT4
441;10k;THT;48.4553;-24.2632;90;Bottom;R52
442;;;125.26;-135.166;0;Bottom;Copper Fill136
443;;;120.193;-133.109;0;Bottom;Copper Fill56
444;;;67.8307;-23.0381;0;Bottom;Copper Fill312
445;;THT;132.275;-69.3482;0;Bottom;PWM 1
446;;;94.1578;-52.5275;0;Bottom;Copper Fill35
447;;;68.9864;-15.7864;0;Bottom;Copper Fill281
448;;;35.7505;-76.0225;0;Bottom;Copper Fill125
449;;;116.205;-63.894;0;Bottom;Copper Fill209
450;;;87.8078;-113.64;0;Bottom;Copper Fill130
451;;;99.5426;-14.1608;0;Bottom;Copper Fill274
452;;;62.4078;-53.1498;0;Bottom;Copper Fill16
453;100nF;100 mil [THT, multilayer];117.67;-96.6532;180;Bottom;C19
454;;;115.303;-123.978;0;Bottom;Copper Fill86
455;;;5.2752;-36.9633;0;Bottom;Via9
456;;DIP (Dual Inline) [THT];94.1753;-94.1132;0;Bottom;LM393-2
457;;;122.758;-67.9072;0;Bottom;Copper Fill210
458;;;29.6418;-138.583;0;Bottom;Copper Fill66
459;;;135.204;-59.449;0;Bottom;Copper Fill217
460;;THT;18.9955;-146.997;90;Bottom;IR1
461;;;35.7505;-76.0225;0;Bottom;Copper Fill382
462;;;122.115;-122.053;0;Bottom;Via5
463;;THT;13.5303;-111.258;0;Bottom;DAC-1
464;;TO220 [THT];61.7903;-70.8722;0;Bottom;Q1
465;;;27.813;-49.0731;0;Bottom;Copper Fill95
466;;;112.014;-54.6738;0;Bottom;Copper Fill231
467;;;62.4078;-55.1564;0;Bottom;Copper Fill300
468;;;115.303;-123.978;0;Bottom;Copper Fill356
469;;;21.9964;-113.475;0;Bottom;Copper Fill158
470;;THT;51.6303;-8.38823;0;Bottom;TH3
471;220;THT;79.5703;-96.0182;90;Bottom;R2
472;68k;THT;42.7403;-92.8432;-90;Bottom;R23
473;;DIP (Dual Inline) [THT];50.9953;-94.7482;0;Bottom;LM393-1
474;;;18.542;-36.8938;0;Bottom;Copper Fill8
475;;;74.3966;-53.6324;0;Bottom;Copper Fill221
476;10k;THT;43.3753;-24.2632;90;Bottom;R49
477;;;89.4207;-23.0381;0;Bottom;Copper Fill38
478;;THT;50.3603;-111.258;0;Bottom;DAC-3
479;47k;THT;40.2003;-92.8432;-90;Bottom;R24
480;0.22mF;200 mil [THT, electrolytic];35.7553;-72.5232;90;Bottom;C20
481;;;117.526;-42.685;0;Bottom;Copper Fill240
482;;;79.5401;-22.1618;0;Bottom;Copper Fill319
483;;;76.8858;-99.1238;0;Bottom;Copper Fill181
484;0.030;5 mm [THT];30.7313;-146.183;90;Bottom;LED1
485;;;56.642;-16.0912;0;Bottom;Copper Fill279
486;;;105.931;-42.7231;0;Bottom;Copper Fill89
487;;300 mil [THT];62.4253;-57.8928;90;Bottom;D1
488;;;47.1678;-61.4302;0;Bottom;Copper Fill18
489;;;55.6514;-23.381;0;Bottom;Copper Fill271
490;;TO220 [THT];136.974;-27.4382;90;Bottom;Q8
491;;;42.9514;-9.3602;0;Bottom;Copper Fill293
492;;;108.42;-127.153;0;Bottom;Copper Fill354
493;;;61.3791;-39.5481;0;Bottom;Copper Fill32
494;;THT;122.75;-10.2932;0;Bottom;RGB2
495;;;126.53;-35.3698;0;Bottom;Copper Fill108
496;;THT;114.495;-127.133;-90;Bottom;LCD
497;100nF;100 mil [THT, multilayer];89.0953;-114.433;0;Bottom;C13
498;;;9.271;-61.1254;0;Bottom;Copper Fill97
499;4.7k;THT;102.426;-30.622;-90;Bottom;R15
500;;;55.8292;-143.32;0;Bottom;Copper Fill144
501;;;34.4678;-119.99;0;Bottom;Copper Fill76
502;22k;THT;52.2653;-60.4582;0;Bottom;R39
503;;;135.89;-36.7922;0;Bottom;Copper Fill254
504;;;50.3682;-49.9748;0;Bottom;Copper Fill232
505;;;22.3266;-49.289;0;Bottom;Copper Fill6
506;;;59.1566;-73.6476;0;Bottom;Copper Fill212
507;;;92.8751;-81.1914;0;Bottom;Copper Fill375
508;;;35.7632;-40.6276;0;Bottom;Copper Fill243
509;100nF;100 mil [THT, multilayer];74.4903;-95.3832;-90;Bottom;C2
510;10k;THT;98.6203;-17.2782;90;Bottom;R17
511;;;22.7584;-66.2054;0;Bottom;Copper Fill326
512;;TO220 [THT];128.084;-38.8682;90;Bottom;Q11
513;;;130.251;-77.483;0;Bottom;Copper Fill202
514;;;11.0998;-34.4046;0;Bottom;Copper Fill253
515;;;70.993;-75.0192;0;Bottom;Copper Fill292
516;;;126.06;-46.0378;0;Bottom;Copper Fill238
517;;THT;57.9803;-12.1982;0;Bottom;Fan-1
518;;;5.9055;-19.6218;0;Bottom;Copper Fill68
519;;TO220 [THT];136.974;-38.8682;90;Bottom;Q7
520;;;15.494;-16.523;0;Bottom;Copper Fill396
521;100nF;100 mil [THT, multilayer];43.3753;-38.873;90;Bottom;C6
522;;;19.1135;-14.7831;0;Bottom;Copper Fill391
523;;;90.3351;-22.1618;0;Bottom;Copper Fill316
524;;TO92 [THT];111.231;-26.9937;90;Bottom;Q16
525;;;25.5778;-16.1547;0;Bottom;Copper Fill91
526;;;116.37;-46.7998;0;Bottom;Copper Fill369
527;;;39.243;-87.7827;0;Bottom;Copper Fill379
528;;;119.329;-89.2686;0;Bottom;Copper Fill190
529;;;20.4978;-16.1547;0;Bottom;Copper Fill121
530;;;41.783;-83.3377;0;Bottom;Copper Fill24
531;;;119.736;-96.6727;0;Bottom;Copper Fill71
532;;;43.6372;-90.6148;0;Bottom;Copper Fill184
533;;;14.5288;-53.2006;0;Bottom;Copper Fill226
534;10k;THT;92.9053;-101.098;180;Bottom;R37
535;0.22mF;200 mil [THT, electrolytic];79.5703;-25.5332;-90;Bottom;C5
536;220;THT;10.9903;-25.5332;180;Bottom;R9
537;;;43.3578;-41.0467;0;Bottom;Copper Fill304
538;;;63.6651;-100.8;0;Bottom;Copper Fill98
539;;;101.194;-96.3044;0;Bottom;Copper Fill1
540;;TO220 [THT];87.1903;-70.8722;0;Bottom;Q3
541;;;119.634;-141.288;0;Bottom;Copper Fill145
542;;;68.7451;-22.1618;0;Bottom;Copper Fill311
543;;;91.2241;-23.0381;0;Bottom;Copper Fill39
544;;;46.2407;-60.5031;0;Bottom;Copper Fill20
545;;;57.8104;-114.44;0;Bottom;Copper Fill150
546;;;109.474;-12.84;0;Bottom;Copper Fill11
547;;;127.165;-124.841;0;Bottom;Copper Fill60
548;;;47.1678;-61.4302;0;Bottom;Copper Fill302
549;0.22mF;200 mil [THT, electrolytic];68.7753;-25.5332;-90;Bottom;C3
550;;;41.402;-55.2834;0;Bottom;Copper Fill230
551;;;94.1578;-62.6875;0;Bottom;Copper Fill44
552;;THT;64.3303;-12.1982;0;Bottom;Fan-2
553;0.22µF;100 mil [THT, electrolytic];127.195;-19.1832;90;Bottom;C22
554;;;62.4078;-38.5575;0;Bottom;Copper Fill31
555;;;34.163;-43.8026;0;Bottom;Copper Fill237
556;;;71.2978;-120.612;0;Bottom;Copper Fill350
557;;;126.53;-46.7998;0;Bottom;Copper Fill370
558;;;26.8478;-64.5417;0;Bottom;Copper Fill53
559;;;13.0048;-41.0086;0;Bottom;Copper Fill245
560;;DIP (Dual Inline) [THT];50.3603;-46.4882;180;Bottom;Mux
561;;;45.72;-13.602;0;Bottom;Copper Fill291
562;;;20.4978;-13.4623;0;Bottom;Copper Fill122
563;;;48.1076;-69.8376;0;Bottom;Copper Fill211

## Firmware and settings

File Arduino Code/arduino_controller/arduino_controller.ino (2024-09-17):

// RGB Fan Controller Arduino code

// BIG CHANGES:
// 1) Remove serial profile sending
// 2) Implement backup to eeprom
// 3) Implement restore from EEPROM + reload conf
// 4) Implement fast FRAM write
// 5) Implement fast RAM read

// Version 143


#include <Wire.h>
//#include <WSWire.h>  // Better I2C library
#include <LCD_I2C.h>
#include <Adafruit_PWMServoDriver.h>
#include <RTClib.h>
#define DECODE_NEC          // Specify decodng protocol, saves loads of memory
#include <IRremote.hpp>

// Some variables that can be changed
const int software_ver = 3;  // Filesystem version
const bool debug = false;  // Enable excessive debug messages

const byte s_ack = 6;  // Acknowledgement byte for serial comms
const byte s_err = 21;  // Error byte for serial comms

#define TWI_FREQ 400000L  // Override default I2C speed

#define btn_bright_up 92
#define btn_bright_down 93
#define btn_pause 65
#define btn_power 64
#define btn_red_1 88
#define btn_green_1 89
#define btn_blue_1 69
#define btn_white_1 68
#define btn_red_2 84
#define btn_green_2 85
#define btn_blue_2 73
#define btn_white_2 72
#define btn_red_3 80
#define btn_green_3 81
#define btn_blue_3 77
#define btn_white_3 76
#define btn_red_4 28
#define btn_green_4 29
#define btn_blue_4 30
#define btn_white_4 31
#define btn_red_5 24
#define btn_green_5 25
#define btn_blue_5 26
#define btn_white_5 27
#define btn_red_up 20
#define btn_green_up 21
#define btn_blue_up 22
#define btn_speed_up 23
#define btn_red_down 16
#define btn_green_down 17
#define btn_blue_down 18
#define btn_speed_down 19
#define btn_diy_1 12
#define btn_diy_2 13
#define btn_diy_3 14
#define btn_auto 15
#define btn_diy_4 8
#define btn_diy_5 9
#define btn_diy_6 10
#define btn_flash 11
#define btn_jump_3 4
#define btn_jump_7 5
#define btn_fade_3 6
#define btn_fade_7 7

#define addr_mux 0x70
#define addr_lcd 0x27
#define addr_eeprom 0x50
#define addr_dac 0x62
#define addr_fram 0x50
#define addr_pwm 0x40
#define addr_rtc 0x68

#define pin_infrared 2
#define pin_rpm 3
#define pin_buzzer 4
#define pin_led 5
#define pin_pwm_enable 6
#define pin_eeprom_wp 7
#define pin_fram_wp 8
#define pin_rpm_inhibit 12
#define pin_rpm_a0 9
#define pin_rpm_a1 10
#define pin_rpm_a2 11
#define pin_builtin_led 13
#define pin_therm_1 A2
#define pin_therm_2 A0
#define pin_therm_3 A6
#define pin_therm_4 A1
#define pin_mux_reset A3
#define pin_ldr A7

// Structs for data
struct task {
  // Scheduling information, default values can be changed
  // Highest priority is chosen when task deadlines clash
  uint8_t function;
  uint8_t priority;
  uint16_t timing;
  uint32_t deadline;
  bool enabled;
} schedule[8] = {
  // Function, priority, timing, deadline, enabled
  {0, 1, 9000, 1500, true},  // Dummy task, default if no tasks enabled
  {1, 6, 100, 1550, true},  // update_led
  {2, 5, 1000, 1600, true},  // adjust_fan
  {3, 4, 150, 1650, true},  // ir_code_update
  {4, 2, 750, 1700, true},  // measure_temps
  {5, 3, 1000, 5000, true},  // lcd_display
  {6, 2, 250, 6000, true},  // read fan RPMs
  {7, 1, 10, 5500, true}  // serial_command
};


// TODO:
// - Allow linking of profiles so that same colour is used for other RGB channels
struct rgb_profile {  // 72 bytes?
  bool power : 1;  // Is RGB channel turned on
  bool pause : 1;  // Is RGB channel paused
  bool use_random : 1; // Use random values for next sequence value
  bool smooth : 1;  // Transition to colours smoothly
  uint8_t link : 2;  // Link to other RGB channels, 2 bits so values 0 (not linked), 1 (link rgb 1), 2 (link rgb 2)
  
  float brightness;  // Brightness multiplier, between 0 and 1
  uint8_t seq_pos;  // Current position in sequence
  uint8_t seq_len;  // Sequence length
  float rate;  // Change rate for transition, between 0 and 1, e.g. 0.1 = 10 steps between colours
  float transition;  // Transition tracking between colours
  uint16_t red[10];  // Red values
  uint16_t green[10];  // Green values
  uint16_t blue[10];  // Blue values
} rgb[3] = {
// pw pa rn smo ln   br   sp sl rat   tr colours
  {1, 0, 0, 0, 0, 0.4, 0, 6, 0.05, 0.0, {4095, 4095, 0, 0, 0, 4095, 0, 0, 0, 0},
                                        {0, 4095, 4095, 4095, 0, 0, 0, 0, 0, 0},
                                        {0, 0, 0, 4095, 4095, 4095, 0, 0, 0, 0}},
  {1, 0, 0, 0, 0, 0.4, 0, 2, 0.05, 0.0, {0, 0, 0, 4095, 0, 0, 0, 0, 0, 0},  // Example of smooth random fade
                                        {0, 0, 0, 4095, 170, 0, 0, 0, 0, 0},
                                        {0, 0, 0, 4095, 0, 170, 0, 0, 0, 0}},
  {1, 0, 0, 0, 0, 0.4, 0, 6, 0.05, 0.0, {4095, 4095, 0, 0, 0, 4095, 0, 0, 0, 0},  // Example of rainbow jump
                                        {0, 4095, 4095, 4095, 0, 0, 0, 0, 0, 0},
                                        {0, 0, 0, 4095, 4095, 4095, 0, 0, 0, 0}},
};

struct fan_profile {  // 32 bytes?
  bool pwm;  // true = pwm (max voltage), false = dc (no PWM)
  bool allow_off;  // true = fan off if temperature below first node, false = does not turn off
  uint16_t max_voltage;  // maximum voltage for fan, such as for 5v compatibility
  uint8_t changerate;  // value to change speed by each update
  uint8_t hysteresis;  // hysteresis in temperature sense, only do something if it changes by 
//                        more than this amount
  int8_t last_temperature;  // records last temperature fan was updated for
  int16_t last_fan_speed;  // records last fan speed, used for smooth speed adjustment
  int16_t target_fan_speed;  // fan speed set by temperature
  int8_t default_temp;  // When temperatures not present, use this as a default value
  // Each temperature multiplied by factor
  // final temperature = sum(multiplied temperatures) / sum(factors)
  // Missing temperatures (PC not connected) and those below -10 (no probe) will be treated as default_temp
  uint8_t factor[8];  // Source temperature factor, bias towards each temperature reading
  int8_t temperature[4];  // Temperature nodes
  int16_t fan_speed[4];  // Fan speed for temperature nodes
} fan[6] = {
// PWM    Off    Volt CR  Hy LT  L_Sp  T_sp  dT   Factor                    Temperature       Fan speed
  {false, true, 4095, 50, 2, 20, 2000, 2000, 50, {1, 2, 0, 0, 0, 0, 0, 0}, {55, 60, 70, 80}, {1600, 1700, 2000, 3500}},
  {false, true, 4095, 50, 2, 20, 2000, 2000, 50, {1, 2, 0, 0, 0, 0, 0, 0}, {55, 60, 70, 80}, {1600, 1700, 2000, 4000}},
  {false, false, 1700, 10, 0, 20, 1400, 1400, 50, {1, 0, 0, 0, 0, 0, 0, 0}, {55, 60, 65, 70}, {600, 900, 1300, 1700}},
  {true, false, 4095, 50, 2, 20, 2000, 2000, 40, {1, 2, 0, 0, 0, 0, 0, 0}, {30, 50, 70, 80}, {1700, 1800, 1850, 1900}},
  {true, false, 4095, 50, 3, 20, 2000, 2000, 50, {2, 2, 2, 2, 0, 0, 0, 0}, {30, 50, 70, 80}, {1000, 2000, 3000, 4000}},
  {true, false, 4095, 50, 3, 20, 2000, 2000, 50, {2, 2, 2, 2, 0, 0, 0, 0}, {30, 50, 70, 80}, {1000, 2000, 3000, 4000}}
};

// Constants
const int mux_pins[] = {pin_rpm_a0, pin_rpm_a1, pin_rpm_a2};
const uint8_t fan_order[] = {6, 7, 0, 5, 3, 4, 1, 2};  // TODO: THIS IS WRONG FIX IT

// FRAM-based variables
uint16_t addr_schedule;
uint16_t addr_gamma;
uint16_t addr_rgb;
uint8_t num_rgb_profiles;
uint16_t addr_fan;
uint8_t num_fan_profiles;
uint16_t addr_strings;
uint8_t strings_length;
uint8_t num_strings;

// Arrays and associated variables
int16_t temperatures[8] = {};  // First 4 are thermistors, last 4 for PC readings
uint32_t fan_rpm[8] = {};  // Array to store fan RPMs
volatile bool rpm_check;  // First trigger may give spurious results, this prevents that
volatile uint32_t fan_time_1 = 0;  // Variables for quick fan RPM measuring
volatile uint32_t fan_time_2 = 0;
volatile uint32_t rpm_current_micros;
volatile uint32_t interrupt_triggers = 0;
int fan_rpm_read = 0;  // Variable to store which fan is being read

// Other variables
uint8_t num_tasks;  // Calculated in setup to identify number of scheduled tasks
uint8_t current_bus;  // Tracks current bus selected in I2C multiplexer
uint8_t display_mode = 1;
uint8_t last_display_mode = 0;
uint16_t light_level = 800;  // Default brightness level, 0 - 1024
uint8_t led_select = 0;  // Which LED channel is selected, 0 = all, 1/2/3 = single RGB channel
bool red_led_override = false;  // Override for red LED, for IR receive light.
uint32_t lcd_timeout = 0;  // Timer for LCD custom message override
uint32_t last_serial_time;  // Used for serial timeout, such as error occurred. Hardcoded 1000ms
uint8_t serial_func;  // Non-blocking serial, records which function currently active
uint8_t serial_sub;  // Used within serial functions to track active section

LCD_I2C lcd(addr_lcd, 16, 2); // Default address of most PCF8574 modules
Adafruit_PWMServoDriver pwm = Adafruit_PWMServoDriver();
//Adafruit_MCP4725 dac;
RTC_PCF8523 rtc;
DateTime current_time;


// TODO: Improve startup, remove 2 second error wait - Display white char for successful init
void setup() {

  bool setup_error = false;
  
  // Set pin modes first to make sure it's all safe
  pinMode(pin_infrared, INPUT);  // IR
  pinMode(pin_rpm, INPUT_PULLUP);  // RPM signal
  pinMode(pin_buzzer, OUTPUT);  // Buzzer
  pinMode(pin_led, OUTPUT);  // Front LED
  pinMode(pin_pwm_enable, OUTPUT);  // PWM Enable
  pinMode(pin_eeprom_wp, OUTPUT);  // EEPROM Write-Protect
  pinMode(pin_fram_wp, OUTPUT);  // FRAM Write-Protect
  pinMode(pin_rpm_inhibit, OUTPUT);  // RPM signal inhibit
  pinMode(pin_rpm_a2, OUTPUT);  // RPM A2
  pinMode(pin_rpm_a1, OUTPUT);  // RPM A1
  pinMode(pin_rpm_a0, OUTPUT);  // RPM A0
  pinMode(pin_builtin_led, OUTPUT);  // Arduino LED
  pinMode(pin_therm_4, INPUT);  // Thermistor 4
  pinMode(pin_therm_2, INPUT);  // Thermistor 2
  pinMode(pin_therm_3, INPUT);  // Thermistor 3
  pinMode(pin_mux_reset, OUTPUT);  // I2C Mux Reset
  // A4 and A5 are I2C pins and don't need to be set here
  pinMode(pin_therm_1, INPUT);  // Thermistor 1
  pinMode(pin_ldr, INPUT);  // LDR

  digitalWrite(pin_builtin_led, HIGH);  // Indicator to let us know the Arduino is starting

  // Set required pins to HIGH. By default, OUTPUTs are low.
  digitalWrite(pin_mux_reset, HIGH);  // I2C Mux resets when this is low, we need it high to work
  digitalWrite(pin_eeprom_wp, HIGH);  // Write-protect EEPROM when high
  digitalWrite(pin_fram_wp, HIGH);  // Write-protect FRAM when high
  digitalWrite(mux_pins[0], HIGH);
  digitalWrite(mux_pins[1], HIGH);
  digitalWrite(mux_pins[2], HIGH);
  digitalWrite(pin_rpm_inhibit, HIGH);  // CD4051 mux needs inhibit high to enable
  
  num_tasks = sizeof(schedule) / sizeof(schedule[0]);  // Calculate number of tasks in schedule
  
  // Set up Serial to communicate with computer if it's listening
  Serial.begin(115200);          // Define baud rate
  while (!Serial);             // Leonardo: wait for serial monitor
  Serial.println(F("RGB Fan Controller Project"));
  Serial.println(F("--------------------------"));
  
  
  Serial.println(F("Init I2C"));
  delay(10);  // A small delay just to make sure the Mux chip is out of reset
  Wire.begin();

  while (true)
  {
    if (check_exists(addr_mux))
    {
      Serial.println(F("Mux OK"));
      break;
    }
    else
    {
      setup_error = true;
      digitalWrite(pin_led, HIGH);
      Serial.println(F("MUX ERR"));
      delay(1000);  // Keep trying to connect, no Mux means no I2C!
      digitalWrite(pin_led, LOW);
      delay(1000);
    }
  }
  digitalWrite(pin_led, LOW);
  digitalWrite(pin_builtin_led, LOW);

  Serial.println(F("Init LCD"));
  delay(10);

  // - CHECK LCD EXISTS!!!!!

  // There seems to be an issue where using select_bus doesn't allow the LCD to initialise properly
  Wire.beginTransmission(addr_mux);  // TCA9548A address is 0x70
  Wire.write(1 << 0);          // send byte to select bus
  Wire.endTransmission();
  if (not check_exists(addr_lcd)) {
    // It is believed that the LCD library has a default mode if no LCD was detected
    setup_error = true;
  }
  
  lcd.begin(false);
  lcd.backlight();
  lcd_clearline(0);
  lcd.print(F("Initialising..."));

  lcd_clearline(1);
  lcd.print(F("PWM - PCA9685"));
  select_bus(6);
  if ( check_exists(0x40) )
  {
    Serial.println(F("PWM OK"));
    pwm.begin();
    pwm.setPWMFreq(1600);
    pwm.setPWM(9, 0, 3000);  // LCD backlight
//    delay(100);  // Delay just so we get to read the message on the LCD
  }
  else {
    setup_error = true;
    display_error(F("PWM - PCA9685"));
  }

  lcd_clearline(0);
  lcd.print(F("Initialising..."));
  lcd_clearline(1);
  lcd.print(F("FRAM"));
  select_bus(6);
  if ( check_exists(addr_pwm) )
  {
    Serial.println(F("FRAM OK"));
    if (not fs_check()) {
//      setup_error = true;
      display_error(F("FRAM VER"));
    }
//    delay(100);  // Delay just so we get to read the message on the LCD
  }
  else {
    setup_error = true;
    display_error(F("FRAM"));
  }


  int8_t found_dac = -1;
  for (int i = 0; i < 4; i++) {
    select_bus(i + 2);
    if ( check_exists(addr_dac) )
    {
      lcd_clearline(0);
      lcd.print(F("Initialising..."));
      Serial.print(F("DAC "));
      Serial.print(i);
      Serial.println(F(" OK"));
      lcd_clearline(1);
      lcd.print(F("DAC - "));
      lcd.print(i);
      found_dac = i;
    }
    else {
      /////////////////
      // It would be nice to send a nice error message with DAC number
      // But I just can't get it to work. This'll have to suffice.
      setup_error = true;
      display_error(F("DAC      "));
    }
  }

  lcd_clearline(0);
  lcd.print(F("Initialising..."));
  lcd_clearline(1);
  lcd.print(F("EEPROM - 24LC256"));
  select_bus(1);
  if ( check_exists(addr_fram) )
  {
    Serial.println(F("EEPROM OK"));
//    delay(100);  // Delay just so we get to read the message on the LCD
  }
  else {
    setup_error = true;
    display_error(F("EEPROM - 24LC256"));
  }

  lcd_clearline(0);
  lcd.print(F("Initialising..."));
  lcd_clearline(1);
  lcd.print(F("RTC - PCF8523"));
  select_bus(7);
  if ( check_exists(addr_rtc) )
  {
    Serial.println(F("RTC OK"));
    rtc.begin();
    // If the clock is on battery, you may not want the clock to be automatically adjusted
    // Move the adjustment into the IF statement to prevent always updating the time
//    rtc.adjust(DateTime(F(__DATE__), F(__TIME__)));
//    Serial.println(F("RTC set"));
    if (!rtc.initialized() or rtc.lostPower()) {
      rtc.adjust(DateTime(F(__DATE__), F(__TIME__)));
      Serial.println(F("RTC set"));
      rtc.start();  // Ensure clock is running
      display_error(F("Clock time lost!"));
    }
    rtc.start();  // Ensure clock is running
//    delay(100);  // Delay just so we get to read the message on the LCD
  }
  else {
    setup_error = true;
    display_error(F("RTC - PCF8523"));
  }

  lcd_clearline(1);
  lcd.print(F("IR Receiver"));
  Serial.println(F("Enable IR"));
  IrReceiver.begin(pin_infrared, false);  // Read up on IR enable_led_feedback
//  delay(100);  // Delay just so we get to read the message on the LCD

  lcd_clearline(1);
  lcd.print(F("RPM Interrupt"));
  attachInterrupt(digitalPinToInterrupt(pin_rpm), rpm_interrupt, RISING);
//  delay(100);

  lcd_clearline(1);
  lcd.print(F("Load Config"));
  load_config();

  // If any errors occurred, don't fully start. Sit here and do nothing.
  if (setup_error == true) {
    lcd.print(F("Error"));
    cmd_halt();  // Use this as a halting function. Will send a serial byte but that's ok
  }

  lcd_clearline(1);
  lcd.print(F("Complete!"));
//  delay(100);  // Delay just so we get to read the message on the LCD

  Serial.println(F("Serial ready"));
  
}

void(* resetFunc) (void) = 0;  // A function which causes a crash, triggers software reset

void loop() {
  // Scheduling
  uint8_t soonest_task = 0;  // Tracks task ID with closest deadline
  uint8_t soonest_priority = 0; // Tracks the priority of this task
  int32_t soonest_deadline = 1000;  // Default delay is 1 second if no tasks
  uint8_t tasks_position = 0;  // Tracks position in list, for updating deadline
  uint32_t cur_time = millis();  // Rolls over after 49 days, probably not an issue
  int32_t task_deadline;  // Time to next deadline, can be negative if we're behind

  /*
     Scheduling:
     [task_id, priority, timing, deadline]

     task_id - task number, used to switch function
     priority - tasks with highest priority win in schedule clash
     timing - how often a task should run, in milliseconds
     deadline - when the task is next due to run
  */

  for (uint8_t i = 0; i < num_tasks; i++)  // For each task
  {
    if (schedule[i].enabled) {
      task_deadline = schedule[i].deadline - cur_time; // Calculate time to deadline
  
      // Update 'soonest' if deadline sooner OR if deadline the same and priority higher
      if ((task_deadline < soonest_deadline) or
          (task_deadline == soonest_deadline and schedule[i].priority > soonest_priority))
      {
        soonest_task = schedule[i].function;
        soonest_priority = schedule[i].priority;
        soonest_deadline = task_deadline;
        tasks_position = i;
      }
    }
  }

  if (soonest_deadline >= 0) {
    if (not red_led_override) {
      digitalWrite(pin_led, LOW);
    }
    
    // If we've got time before the next task deadline
    delay(soonest_deadline);  // Sleep until time required
  }
  else if (soonest_deadline > -5) {
    // If we're slightly behind on task deadline, try tweaking the deadline slightly
    // to avoid this happening again. Should spread tasks out so they don't all occur at the
    // same time and cause this to happen.
    schedule[tasks_position].deadline += 1;  // Shift deadline to try and avoid future conflicts
  }
  else {
    digitalWrite(pin_led, HIGH);
    
    // When we're behind, we set the deadline to now, so that it is put safely into the future
    // If we've missed a couple of tasks, rushing them won't achieve much
    // This also helps stop an endless loop of a task failing to catch up
    if (debug) {
      Serial.print(F("Task behind: "));  // We are running behind more than expected!
      Serial.print(tasks_position);
      Serial.print(F(", time: "));
      Serial.println(soonest_deadline);
    }
    schedule[tasks_position].deadline = cur_time;
  }
  
  schedule[tasks_position].deadline += schedule[tasks_position].timing; // Update task deadline

  uint32_t task_time = micros();  // Track how long each task took to execute

  switch (soonest_task)
  {
    case 0: break;  // Default task, do nothing
    case 1:
      update_leds(); break;
    case 2:
      adjust_fans(); break;
    case 3:
      ir_receive(); break;
    case 4:
      measure_sensors(); break;
    case 5:
      update_display(); break;
    case 6:
      read_rpm(); break;
    case 7:
      serial_command(); break;
    default:
      Serial.println(F("Un Func")); break;
  }

  // Function to print out any slow tasks taking over 1ms to complete
  uint32_t task_time_end = micros();
  task_time = task_time_end - task_time;
  if (task_time > 1000 and debug) {
    Serial.print(F("Task uS: "));
    Serial.print(soonest_task);
    Serial.print(F(", "));
    Serial.println(task_time);
  }
}



void serial_command() {
  // Main function for handling serial communications with PC

  byte check_byte;
  byte read_byte;
  
  if (serial_func == 0) {
    if (not red_led_override) {
      digitalWrite(pin_led, LOW);
    }
    
    if (Serial.available() >= 2) {
      // Serial trigger format with error checking
      // check byte which is (255 - function code)
      // read byte for function code
      // When added, result should be 255
      check_byte = Serial.read();
      read_byte = Serial.read();
  
      if (check_byte + read_byte != 255) {
        // If we have an error, send a nack and return
        Serial.write(s_err);
        return;
      }
      else {
        serial_func = read_byte;
        serial_sub = 0;
        digitalWrite(pin_led, HIGH);
        last_serial_time = millis();
      }
    }
    else {
      // Return if there is nothing to do, prevent infinite error in switch statement
    return;
    }
  }
  else {
    if (Serial.available() > 0) {
      // If we have serial communication, update last_serial_time
      last_serial_time = millis();
    }
    else if (millis() > last_serial_time + 1000) {
      // If we haven't had a serial update in 1000ms
      // Force reset the serial so it doesn't just stay stuck
      serial_func = 0;
    }
  }

  switch (serial_func) {
    case 1:  // Halt
      cmd_halt();
      break;
    case 2:  // Alive
      cmd_alive();
      break;
    case 3:  // Load Config
      cmd_load_config();
      break;
    case 4:  // Write FRAM
      cmd_write_fram();
      break;
    case 5:  // Write temperature
      cmd_write_temp();
      break;
//    case 6:  // Write RGB
//      cmd_write_rgb();
//      break;
    case 7:  // Write clock time
      cmd_write_rtc();
      break;
//    case 8:  // Write fan profile
//      cmd_write_fan();
//      break;
    case 9:  // Write LCD message
      cmd_write_lcd();
      break;
    case 10:  // Read RPM
      cmd_read_rpm();
      break;
    case 11:  // Read temperature
      cmd_read_temp();
      break;
    case 12:  // Read FRAM
      cmd_read_fram();
      break;
    case 13:  // Set pins
      cmd_set_pins();
      break;
    case 14:  // FRAM backup
      cmd_backup_fram();
      break;
    case 15:  // FRAM restore
      cmd_restore_fram();
      break;
    case 16:  // FRAM fast write
      cmd_fastwrite_fram();
      break;
    case 17:  // FRAM fast read
      cmd_fastread_fram();
      break;
    default:  // Not recognised
      Serial.write(s_err);
      serial_func = 0;
      break;
  }
}

void cmd_halt() {
  // Infinite loop to halt the Arduino, flashes light to indicate halted
  
  while (true) {
    digitalWrite(pin_led, HIGH);
    delay(500);
    digitalWrite(pin_led, LOW);
    delay(500);
  }
  serial_func = 0;  // Reset serial to begin new function
}
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

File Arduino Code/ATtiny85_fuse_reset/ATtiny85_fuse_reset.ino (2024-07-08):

// AVR High-voltage Serial Fuse Reprogrammer

// https://www.electronics-lab.com/recover-bricked-attiny-using-arduino-as-high-voltage-programmer/

// Baud rate 19200, no line ending


 // Adapted from code and design by Paul Willoughby 03/20/2010
 // http://www.rickety.us/2010/03/arduino-avr-high-voltage-serial-programmer/
 // Fuse Calc:
 // http://www.engbedded.com/fusecalc/

 #define RST 13 // Output to level shifter for !RESET from transistor
 #define SCI 12 // Target Clock Input
 #define SDO 11 // Target Data Output
 #define SII 10 // Target Instruction Input
 #define SDI 9 // Target Data Input
 #define VCC 8 // Target VCC

 #define HFUSE 0x747C
 #define LFUSE 0x646C
 #define EFUSE 0x666E

 // Define ATTiny series signatures
 #define ATTINY13 0x9007 // L: 0x6A, H: 0xFF 8 pin
 #define ATTINY24 0x910B // L: 0x62, H: 0xDF, E: 0xFF 14 pin
 #define ATTINY25 0x9108 // L: 0x62, H: 0xDF, E: 0xFF 8 pin
 #define ATTINY44 0x9207 // L: 0x62, H: 0xDF, E: 0xFFF 14 pin
 #define ATTINY45 0x9206 // L: 0x62, H: 0xDF, E: 0xFF 8 pin
 #define ATTINY84 0x930C // L: 0x62, H: 0xDF, E: 0xFFF 14 pin
 #define ATTINY85 0x930B // L: 0x62, H: 0xDF, E: 0xFF 8 pin

 void setup() {
 pinMode(VCC, OUTPUT);
 pinMode(RST, OUTPUT);
 pinMode(SDI, OUTPUT);
 pinMode(SII, OUTPUT);
 pinMode(SCI, OUTPUT);
 pinMode(SDO, OUTPUT); // Configured as input when in programming mode
 digitalWrite(RST, HIGH); // Level shifter is inverting, this shuts off 12V
 Serial.begin(19200);
 Serial.println("Code is modified by Rik. Visit riktronics.wordpress.com and electronics-lab.com for more projects");
 Serial.println("-------------------------------------------------------------------------------------------------");
 Serial.println("Enter any character to start process..");}


 void loop() {
 if (Serial.available() > 0) {
 Serial.read();
 pinMode(SDO, OUTPUT); // Set SDO to output
 digitalWrite(SDI, LOW);
 digitalWrite(SII, LOW);
 digitalWrite(SDO, LOW);
 digitalWrite(RST, HIGH); // 12v Off
 digitalWrite(VCC, HIGH); // Vcc On
 delayMicroseconds(20);
 digitalWrite(RST, LOW); // 12v On
 delayMicroseconds(10);
 pinMode(SDO, INPUT); // Set SDO to input
 delayMicroseconds(300);
 unsigned int sig = readSignature();
 Serial.println("Reading signature from connected ATtiny......");
 Serial.println("Reading complete..");
 Serial.print("Signature is: ");
 Serial.println(sig, HEX);
 readFuses();
 if (sig == ATTINY13) {

 Serial.println("The ATtiny is detected as ATtiny13/ATtiny13A..");
 Serial.print("LFUSE: ");
 writeFuse(LFUSE, 0x6A);
 Serial.print("HFUSE: ");
 writeFuse(HFUSE, 0xFF);
 Serial.println("");
 } else if (sig == ATTINY24 || sig == ATTINY44 || sig == ATTINY84 ||
 sig == ATTINY25 || sig == ATTINY45 || sig == ATTINY85) {

 Serial.println("The ATtiny is detected as "); 
 if(sig == ATTINY24) Serial.println("ATTINY24..");
 else if(sig == ATTINY44) Serial.println("ATTINY44..");
 else if(sig == ATTINY84) Serial.println("ATTINY84..");
 else if(sig == ATTINY25) Serial.println("ATTINY25..");
 else if(sig == ATTINY45) Serial.println("ATTINY45..");
 else if(sig == ATTINY85) Serial.println("ATTINY85..");
 
 writeFuse(LFUSE, 0x62);
 writeFuse(HFUSE, 0xDF);
 writeFuse(EFUSE, 0xFF);
 }

 Serial.println("Fuses will be read again to check if it's changed successfully..");
 readFuses();
 digitalWrite(SCI, LOW);
 digitalWrite(VCC, LOW); // Vcc Off
 digitalWrite(RST, HIGH); // 12v Off

 Serial.println("");
 Serial.println("");
 Serial.println("");
 Serial.println("");
 }
 }

 byte shiftOut (byte val1, byte val2) {
 int inBits = 0;
 //Wait until SDO goes high
 while (!digitalRead(SDO))
 ;
 unsigned int dout = (unsigned int) val1 << 2;
 unsigned int iout = (unsigned int) val2 << 2;
 for (int ii = 10; ii >= 0; ii--) {
 digitalWrite(SDI, !!(dout & (1 << ii)));
 digitalWrite(SII, !!(iout & (1 << ii)));
 inBits <<= 1; inBits |= digitalRead(SDO);
 digitalWrite(SCI, HIGH);
 digitalWrite(SCI, LOW);
 } 
 return inBits >> 2;
 }

 void writeFuse (unsigned int fuse, byte val) {
 
 Serial.println("Writing correct fuse settings to ATtiny.......");
 
 shiftOut(0x40, 0x4C);
 shiftOut( val, 0x2C);
 shiftOut(0x00, (byte) (fuse >> 8));
 shiftOut(0x00, (byte) fuse);

 Serial.println("Writing complete..");
 }

 void readFuses () {

 Serial.println("Reading fuse settings from connected ATtiny.......");
 
 byte val;
 shiftOut(0x04, 0x4C); // LFuse
 shiftOut(0x00, 0x68);
 val = shiftOut(0x00, 0x6C);
 Serial.print("LFuse: ");
 Serial.print(val, HEX);
 shiftOut(0x04, 0x4C); // HFuse
 shiftOut(0x00, 0x7A);
 val = shiftOut(0x00, 0x7E);
 Serial.print(", HFuse: ");
 Serial.print(val, HEX);
 shiftOut(0x04, 0x4C); // EFuse
 shiftOut(0x00, 0x6A);
 val = shiftOut(0x00, 0x6E);
 Serial.print(", EFuse: ");
 Serial.println(val, HEX);
 Serial.println("Reading complete..");
 }

 unsigned int readSignature () {
 unsigned int sig = 0;
 byte val;
 for (int ii = 1; ii < 3; ii++) {
 shiftOut(0x08, 0x4C);
 shiftOut( ii, 0x0C);
 shiftOut(0x00, 0x68);
 val = shiftOut(0x00, 0x6C);
 sig = (sig << 8) + val;
 }
 return sig;
 }

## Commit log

2024-07-08 Fritzing PCB files v3 6.3.4
    This is the latest revision of the circuit board that I am using.
    [Controller_v3 - trial 6.3.4 mux fix filled.fzz, Controller_v3 - trial 6.3.4 mux fix prep.fzz]
2024-07-08 Add files via upload
    Fritzing PCB files in a directory.
    [Controller_v3 - trial 6.3.4 mux fix filled.fzz, Controller_v3 - trial 6.3.4 mux fix prep.fzz]
2024-07-08 Rename IMG_20230830_135151640.jpg to Semi-Populated PCB.jpg
2024-09-17 Add PCB files and images
    [Controller_v3 - trial 6.3.4 mux fix filled_contour.gm1, Controller_v3 - trial 6.3.4 mux fix filled_copperBottom.gbl, Controller_v3 - trial 6.3.4 mux fix filled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]
